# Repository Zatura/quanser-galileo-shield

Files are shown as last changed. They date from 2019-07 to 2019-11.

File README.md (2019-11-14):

# quanser_galileo_shield
Controlling a high-power quanser robotic arm with a hand-made Galileo compatible shield.  
PCB project design and simulation were made using proteus  https://www.labcenter.com/pcb/  
Shield Schematic  
Report (portuguese)  
  
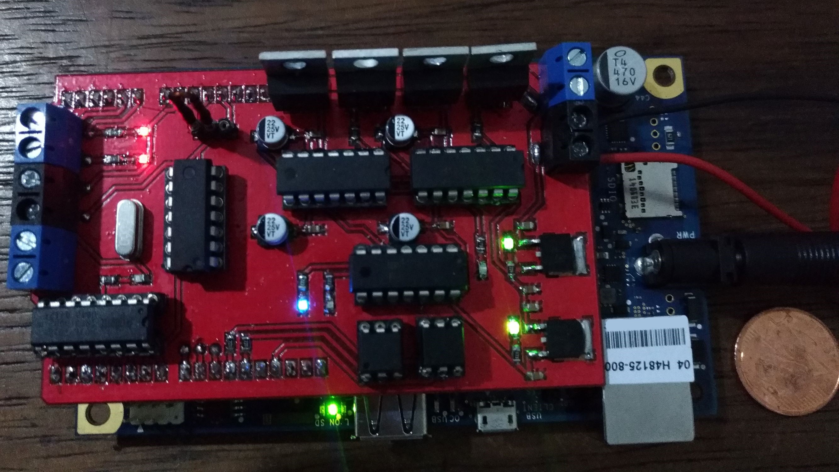
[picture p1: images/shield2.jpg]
shield
 

### Bare Copper PCB  
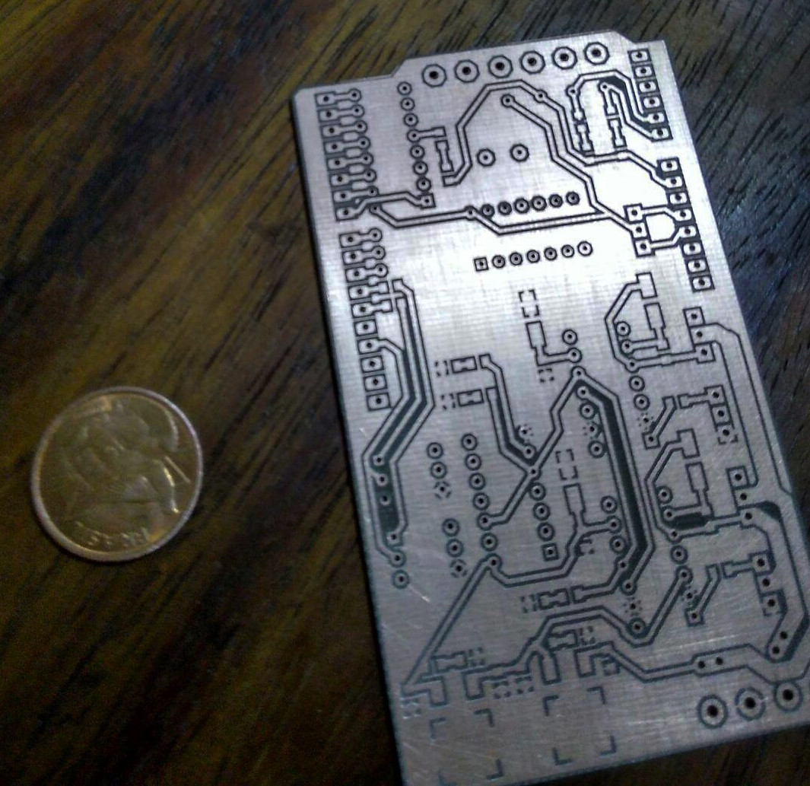
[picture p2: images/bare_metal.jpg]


### UV Masking(red tint)   
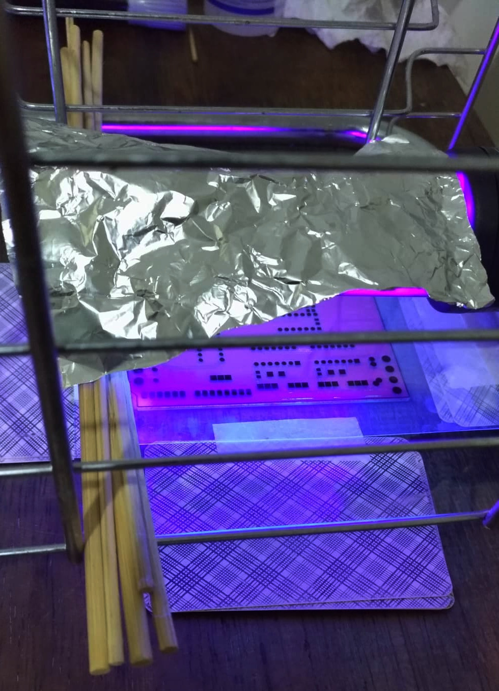
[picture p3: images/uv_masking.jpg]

  
# Use and Compilation
Compile using `make`  
After compilation success, executable `qmotion` should be at `/bin` folder 
 
```
qmotion - quanser motion

USAGE
	qmotion [options] input file

DESCRIPTION
	qmotion is a quanser robotic arm controller

OPTIONS
	-v, --version
		Prints qmotion version
    
	-h, --help
		Prints this help message

	-m VOLTAGE TIME, --move VOLTAGE TIME
		Moves the quanser robotic arm using VOLTAGE(-27 to 27) during TIME seconds 

	-t ANGLE, --target ANGLE 
		Moves the quanser robotic arm to the target at ANGLE degrees 

	-d, --decoder
		Reads and shows decoder and limit switch status

	-r, --reset
		Resets decoder register

	-p P I D, --pid P I D 
		Sets Proportional(P), Integrative(I) and Derivative(D) gains, saved at pid.dat file
    
	--no-color
		Does not use colors for printing
```    
    
# Examples

https://link.springer.com/content/pdf/10.1007/978-1-4302-6838-3_14.pdf

# Pins

IO0: D7 (encoder bit 7)  
IO1: D6 (encoder bit 6)  
IO2: D5 (encoder bit 5)  
IO3: D4 (encoder bit 4)  
IO4: D3 (encoder bit 3)  
IO5: D2 (encoder bit 2)  
IO6: D1 (encoder bit 1)  
IO7: D0 (encoder bit 0)  

IO8 :  !RST (Reset for 16-bits encoder register)  
IO9 :  !OE (Enable, activates the tristate buffer from the register)  
IO10 :  SEL (Selector for 16-bits encoder high or low byte in register)  
IO11:  PWM (pulse modulation width)  
IO12: SD (bridge-drivers shutdown)  
IO14: LMT_SWT2 (arm limit-sensor input)  
IO15: LMT_SWT1 (arm limit-sensor input)

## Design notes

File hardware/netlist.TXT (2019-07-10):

ISIS SCHEMATIC DESCRIPTION FORMAT 8.0
=====================================
Design:   H-bridge
Doc. no.: <NONE>
Revision: <NONE>
Author:   Arthur, Daniel e Matheus
Created:  25/06/2019
Modified: 25/06/2019

*PROPERTIES,0    

*MODELDEFS,0    

*PARTLIST,67   
A,LED-BLUE,LED-BLUE,BV=4V,DRIVE=1,EID=25,IMAX=30mA,PACKAGE=0805,ROFF=100k,RS=3,TLITMIN=0.1m,VF=3V
B,LED-BLUE,LED-BLUE,BV=4V,DRIVE=1,EID=24,IMAX=30mA,PACKAGE=0805,ROFF=100k,RS=3,TLITMIN=0.1m,VF=3V
C1,PCELEC22U16V75M,22uF,CODE="Digikey P5135-ND",EID=20,PACKAGE=ELECT-5
C2,CAP,100nF,EID=5,PACKAGE=0805_CAP
C3,CAP,100nF,EID=8,PACKAGE=0805_CAP
C4,PCELEC22U16V75M,22uF,CODE="Digikey P5135-ND",EID=22,PACKAGE=ELECT-5
C5,PCELEC22U16V75M,22uF,CODE="Digikey P5135-ND",EID=E,PACKAGE=ELECT-5
C6,CAP,100nF,EID=F,PACKAGE=0805_CAP
C7,CAP,100nF,EID=4,PACKAGE=0805_CAP
C8,PCELEC22U16V75M,22uF,CODE="Digikey P5135-ND",EID=B,PACKAGE=ELECT-5
C9,CAP,330nF,EID=3E,PACKAGE=0805_CAP
C10,CAP,100nF,EID=3F,PACKAGE=0805_CAP
C11,CAP,330nF,EID=41,PACKAGE=0805_CAP
C12,CAP,100nF,EID=40,PACKAGE=0805_CAP
C13,CERAMIC22P,22pF,CODE="Maplin WX48C",EID=2B,PACKAGE=0805_CAP
C14,CERAMIC22P,22pF,CODE="Maplin WX48C",EID=2C,PACKAGE=0805_CAP
D1,1N4007,1N4007,EID=1,PACKAGE=DO214
D2,1N4007,1N4007,EID=C,PACKAGE=DO214
D3,LED-GREEN,LED-GREEN,BV=4V,DRIVE=1,EID=44,IMAX=20mA,PACKAGE=0805,ROFF=100k,RS=3,TLITMIN=0.1m,VF=2V
D4,LED-GREEN,LED-GREEN,BV=4V,DRIVE=1,EID=43,IMAX=20mA,PACKAGE=0805,ROFF=100k,RS=3,TLITMIN=0.1m,VF=2V
J1,ARDUINO-SIL8,ARDUINO-SIL8,EID=4F,PACKAGE=ARDUINO-SIL8
J2,ARDUINO-SIL10,ARDUINO-SIL10,EID=52,PACKAGE=ARDUINO-SIL10
J3,ARDUINO-SIL6,ARDUINO-SIL6,EID=50,PACKAGE=ARDUINO-SIL6
J4,ARDUINO-SIL8,ARDUINO-SIL8,EID=51,PACKAGE=ARDUINO-SIL8
J5,TBLOCK-M2,TBLOCK-M2,EID=18,PACKAGE=TBLOCK-M2
J6,TBLOCK-M2,TBLOCK-M2,EID=16,PACKAGE=TBLOCK-M2
J6_MOTOR,TBLOCK-M2,TBLOCK-M2,EID=29,PACKAGE=TBLOCK-M2
J7,TBLOCK-M2,TBLOCK-M2,EID=26,PACKAGE=TBLOCK-M2
J8,TBLOCK-M2,TBLOCK-M2,EID=10,PACKAGE=TBLOCK-M2
JP1,JUMPER2,JUMPER2,EID=2E,PACKAGE=CONN-SIL3,ROFF=100M,RON=0.01,STATE=0,TSWITCH=1m
LMT1,LED-GREEN,LED-RED,BV=4V,DRIVE=1,EID=1A,IMAX=20mA,PACKAGE=0805,ROFF=100k,RS=3,TLITMIN=0.1m,VF=2V
LMT2,LED-GREEN,LED-RED,BV=4V,DRIVE=1,EID=4B,IMAX=20mA,PACKAGE=0805,ROFF=100k,RS=3,TLITMIN=0.1m,VF=2V
Q1,IRFZ44N,IRFZ44N,EID=11,PACKAGE=TO220,SPICELIB=IRPOWER,SPICEMODEL=irfz44n,SPICEPINS="D,G,S"
Q2,IRFZ44N,IRFZ44N,EID=12,PACKAGE=TO220,SPICELIB=IRPOWER,SPICEMODEL=irfz44n,SPICEPINS="D,G,S"
Q3,IRFZ44N,IRFZ44N,EID=19,PACKAGE=TO220,SPICELIB=IRPOWER,SPICEMODEL=irfz44n,SPICEPINS="D,G,S"
Q4,IRFZ44N,IRFZ44N,EID=1F,PACKAGE=TO220,SPICELIB=IRPOWER,SPICEMODEL=irfz44n,SPICEPINS="D,G,S"
R1,RES,10R,EID=14,PACKAGE=0805_RES,PRIMTYPE=RESISTOR
R2,RES,10R,EID=15,PACKAGE=0805_RES,PRIMTYPE=RESISTOR
R3,RES,10R,EID=9,PACKAGE=0805_RES,PRIMTYPE=RESISTOR
R4,RES,10R,EID=6,PACKAGE=0805_RES,PRIMTYPE=RESISTOR
R5,RES,220KR,EID=45,PACKAGE=0805_RES,PRIMTYPE=RESISTOR
R6,RES,47KR,EID=42,PACKAGE=0805_RES,PRIMTYPE=RESISTOR
R7,RES,10KR,EID=4D,PACKAGE=0805_RES,PRIMTYPE=RESISTOR
R8,RES,1MR,EID=2D,PACKAGE=0805_RES,PRIMTYPE=RESISTOR
R9,RES,10kR,EID=13,PACKAGE=0805_RES,PRIMTYPE=RESISTOR
R11,RES,10kR,EID=17,PACKAGE=0805_RES,PRIMTYPE=RESISTOR
R13,RES,47KR,EID=1B,PACKAGE=0805_RES,PRIMTYPE=RESISTOR
R14,RES,47KR,EID=1E,PACKAGE=0805_RES,PRIMTYPE=RESISTOR
R15,RES,22KR,EID=21,PACKAGE=0805_RES,PRIMTYPE=RESISTOR
R16,RES,22KR,EID=23,PACKAGE=0805_RES,PRIMTYPE=RESISTOR
R19,RES,220R,EID=28,PACKAGE=0805_RES,PRIMTYPE=RESISTOR
R20,RES,220R,EID=32,PACKAGE=0805_RES,PRIMTYPE=RESISTOR
R23,RES,10KR,EID=2A,PACKAGE=0805_RES,PRIMTYPE=RESISTOR
R24,RES,470kR,EID=49,PACKAGE=0805_RES,PRIMTYPE=RESISTOR
R25,RES,470kR,EID=4A,PACKAGE=0805_RES,PRIMTYPE=RESISTOR
RST,LED-GREEN,LED-GREEN,BV=4V,DRIVE=1,EID=1C,IMAX=20mA,PACKAGE=0805,ROFF=100k,RS=3,TLITMIN=0.1m,VF=2V
SD,LED-GREEN,LED-GREEN,BV=4V,DRIVE=1,EID=4C,IMAX=20mA,PACKAGE=0805,ROFF=100k,RS=3,TLITMIN=0.1m,VF=2V
U1,IR2110,IR2110,EID=A,ITFMOD=IR2112ITF,PACKAGE=DIL14
U2,IR2110,IR2110,EID=D,ITFMOD=IR2112ITF,PACKAGE=DIL14
U3,7812,7812,EID=3D,PACKAGE=DPAK
U4,7805,7805,EID=3C,PACKAGE=DPAK
U5,74LS04,74LS04,EID_E=7,GND=GND3,ITFMOD=TTLLS,PACKAGE=DIL14,VCC=VDD_GALILEO
U7,4N25,4N25,EID=2,PACKAGE=DIL06
U8,4N25,4N25,EID=3,PACKAGE=DIL06
U9,74LS04,74LS04,EID_A=35,EID_C=39,EID_D=36,ITFMOD=TTLLS,MODFILE=74INV.MDF,PACKAGE=DIL14
U10,HCTL2016,HCTL2016,EID=1D,PACKAGE=DIL16
X1,CRYSTAL,CRYSTAL,EID=27,FREQ=1MHz,PACKAGE=XTAL18

*NETLIST,71   
#00000,6
C3,PS,2
C4,PS,-
Q1,PS,3
Q2,PS,2
J6_MOTOR,PS,1
U1,PS,5

#00001,4
C3,PS,1
D1,PS,K
U1,PS,6
C4,PS,+

#00008,2
R1,PS,1
U1,PS,7

#00009,2
R1,PS,2
Q1,PS,1

#00010,2
R2,PS,1
U1,PS,1

#00011,2
R2,PS,2
Q2,PS,1

#00012,6
Q3,PS,2
Q4,PS,3
C8,PS,-
C7,PS,2
U2,PS,5
J6_MOTOR,PS,2

#00013,2
Q3,PS,1
R3,PS,2

#00014,2
Q4,PS,1
R4,PS,2

#00018,4
C7,PS,1
D2,PS,K
U2,PS,6
C8,PS,+

#00023,2
R4,PS,1
U2,PS,7

#00024,2
R3,PS,1
U2,PS,1

#00030,2
R7,PS,1
LMT1,PS,1

#00036,2
R23,PS,1
LMT2,PS,1

#00044,2
R6,PS,1
D4,PS,1

#00045,2
D3,PS,1
R5,PS,2

#00051,2
U7,PS,1
R19,PS,2

#00054,3
U7,PS,5
R9,PS,2
U9,IP,13

#00055,2
U7,PS,6
R24,PS,1

#00057,2
U8,PS,1
R20,PS,2

#00060,3
U8,PS,5
R11,PS,2
U9,IP,1

#00061,2
U8,PS,6
R25,PS,1

#00066,2
R13,PS,1
SD,PS,1

#00068,2
R14,PS,1
RST,PS,1

#00070,2
R15,PS,1
B,PS,1

#00071,2
R16,PS,1
A,PS,1

#00110,1
J3,PS,3

#00111,1
J3,PS,4

#00112,1
J3,PS,5

#00113,1
J3,PS,6

#00114,1
J4,PS,1

#00115,1
J4,PS,2

#00116,1
J4,PS,3

#00119,1
J4,PS,6

#00121,1
J4,PS,8

#00126,1
J2,PS,1

#00127,1
J2,PS,2

#00128,1
J2,PS,3

#00130,1
J2,PS,5

#00132,4
X1,PS,1
C13,PS,2
R8,PS,1
U5,IP,11

SOURCE_12,10
SOURCE_12,OT
U4,IP,2
C11,PS,2
U3,PS,3
C10,PS,2
R5,PS,1
D2,PS,A
U2,PU,3
D1,PS,A
U1,PU,3

SOURCE_27,6
SOURCE_27,OT
J8,PS,2
U3,IP,2
C9,PS,2
Q4,PS,2
Q1,PS,2

A,6
A,OT
R16,PS,2
U9,IP,5
U9,OP,12
U2,IP,10
U1,IP,12

B,5
B,OT
R15,PS,2
U9,OP,6
U2,IP,12
U1,IP,10

{NC},8
U8,PS,3
U7,PS,3
U2,PS,4
U2,PS,8
U2,PS,14
U1,PS,4
U1,PS,8
U1,PS,14

SD,5
SD,OT
R13,PS,2
U9,OP,2
U2,IP,11
U1,IP,11

D0,3
D0,OT
J1,PS,1
U10,OP,1

D1,3
D1,OT
J1,PS,2
U10,OP,15

D2,3
D2,OT
J1,PS,3
U10,OP,14

D3,3
D3,OT
J1,PS,4
U10,OP,13

D4,3
D4,OT
J1,PS,5
U10,OP,12

D5,3
D5,OT
J1,PS,6
U10,OP,11

D6,3
D6,OT
J1,PS,7
U10,OP,10

D7,3
D7,OT
J1,PS,8
U10,OP,9

LMT2,4
LMT2,OT
J3,PS,1
R23,PS,2
J6,PS,2

LMT1,4
LMT1,OT
J3,PS,2
R7,PS,2
J6,PS,1

OE,3
OE,OT
J2,PS,9
U10,IP,4

RST,4
RST,OT
J2,PS,10
U10,IP,5
R14,PS,2

GPIO_PWM,3
GPIO_PWM,OT
J2,PS,7
R19,PS,1

SEL,3
SEL,OT
J2,PS,8
U10,IP,3

GPIO_SD,3
GPIO_SD,OT
J2,PS,6
R20,PS,1

CLK,6
CLK,OT
X1,PS,2
C14,PS,2
R8,PS,2
U5,OP,10
U10,IP,2

CH A,3
CH A,OT
J5,PS,1
U10,IP,7

CH B,3
CH B,OT
J5,PS,2
U10,IP,6

VDD5,3
VDD5,OT
JP1,PS,1
J4,PS,5

VDD3,3
VDD3,OT
JP1,PS,3
J4,PS,4

GND,28,CLASS=GND
GND,PR
R25,PS,2
R24,PS,2
U9,PP,7
B,PS,2
A,PS,2
SD,PS,2
U8,PS,4
U7,PS,4
J8,PS,1
U3,PP,1
C9,PS,1
C10,PS,1
D3,PS,2
U4,PP,1
C11,PS,1
C12,PS,1
D4,PS,2
C5,PS,-
C6,PS,2
U2,PP,13
U2,PP,2
C1,PS,-
C2,PS,2
U1,PP,13
Q2,PS,3
Q3,PS,3
U1,PP,2

GND2,4,CLASS=GND
GND2,PR
J2,PS,4
U8,PS,2
U7,PS,2

GND3,10,CLASS=GND
GND3,PR
J7,PS,1
U5,PP,7
C13,PS,1
C14,PS,1
J4,PS,7
U10,IP,8
RST,PS,2
LMT2,PS,2
LMT1,PS,2

VCC/VDD,15,CLASS=POWER
VCC,PT
VCC/VDD,PR
SOURCE_5,OT
U9,PP,14
R11,PS,1
R9,PS,1
U4,PS,3
C12,PS,2
R6,PS,2
C5,PS,+
C6,PS,1
U2,PP,9
C1,PS,+
C2,PS,1
U1,PP,9

VDD_GALILEO,5,CLASS=GND
VDD_GALILEO,PR
JP1,PS,2
J7,PS,2
U5,PP,14
U10,IP,16

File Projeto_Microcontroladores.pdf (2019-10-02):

## Confecçao de um Shield para a Galileo Gen 2 para o ˜ Acionamento das Juntas e Leitura dos Sensores do Robô 2DSFJE

Arthur Ribeiro¹

, Daniel Cunha¹

, Matheus Tura¹

1
Instituto de Informatica – Universidade Federal do Rio Grande do Sul (UFRGS) ´ Caixa Postal 15.064 – 91.501-970 – Porto Alegre – RS – Brazil

{aribeiro, dmcunha, mttura}@inf.ufrgs.br

Resumo. Este documento descreve o processo para a criaçao de um shield para ˜ a placa Intel Galileo Gen 2. Este hardware e capaz de acionar o motor e ler os ´
sensores presentes no robo Quanser 2DSFJE. Ao longo do documento ser ˆ | a des- ´
crito o processo de todas as etapas de desenvolvimento deste hardware, desde
de sua etapa inicial de concepçao at ˜ | e a etapa final de implementaç ´ | ao. ˜

### 1. Introduçaõ

O projeto proposto consiste no desenvolvimento e confecçao de um shield para a Intel Ga- ˜ lileo Gen 2, o shield deve ser capaz de acionar uma das juntas do robo Quanser 2DSFJE, a ˆ
junta possui um motor com encoder, para o acionamento e necess ´ | ario fornecer uma tens ´ | aõ
entre -27 e 27 volts, o shield deve implementar uma ponte h que controla o valor medio ´
desta tensao atrav ˜ | es de um sinal pwm. O ciclo de trabalho deste pwm representa o sen- ´
tido e velocidade do movimento do motor, onde o ciclo de trabalho em 0% corresponde ao motor girando em velocidade maxima em um sentido, o ciclo de trabalho em 50% ´ corresponde ao motor parado, o ciclo de trabalho em 100% corresponde ao motor girando
em velocidade maxima no sentido contr ´ | ario. O encoder do Quanser tamb ´ | em deve ser ´
decodificado pelo shield, para decodificar quadratura, foi utilizado um circuito integrado decodificador de quadratura, para que nao haja erro na contagem e consequentemente ˜ dados inconsistentes.

Concomitantemente com o desenvolvimento do shield, deve-se desenvolver um software que implemente um controlador PID. O software deve incluir uma biblioteca com uma API. Com a API deve ser possível ler o valor do encoder em radianos, comandar do motor em Volts e a leitura do sensor de fim de curso. A biblioteca deve ser desenvolvida para executar no Linux como um programa no espaço de usuario, sem pri- ´
vilegios de superusu ´ | ario. Os pr ´ | oximos cap ´ | ítulos detalharao o funcionamento do hardware ˜
e do software desenvolvido.

### 2. Hardware

Para possibilitar o controle a junta do Quanser utilizando a Galileo Gen 2, se desenvolveu um shield utilizando uma placa de circuito impresso. O shield possui dois circuitos distintos, um deles implementa uma ponte H que possui toda parte de alta potencia do shield, o outro circuito implementa o decodificador de quadratura.

Alem disso, para maior parte do circuito foi optado por componentes SMD, devido ´ ao seu menor tamanho e tambem menores problemas de mal contato, e praticidade na hora ´

da soldagem. O tamanho escolhido de SMDS para capacitores, resistores e LEDs foi de 0805, nao foi escolhido abaixo deste tamanho, pois abaixo desse tamanho a dificuldade ˜ de solda poderia aumentar consideravelmente.

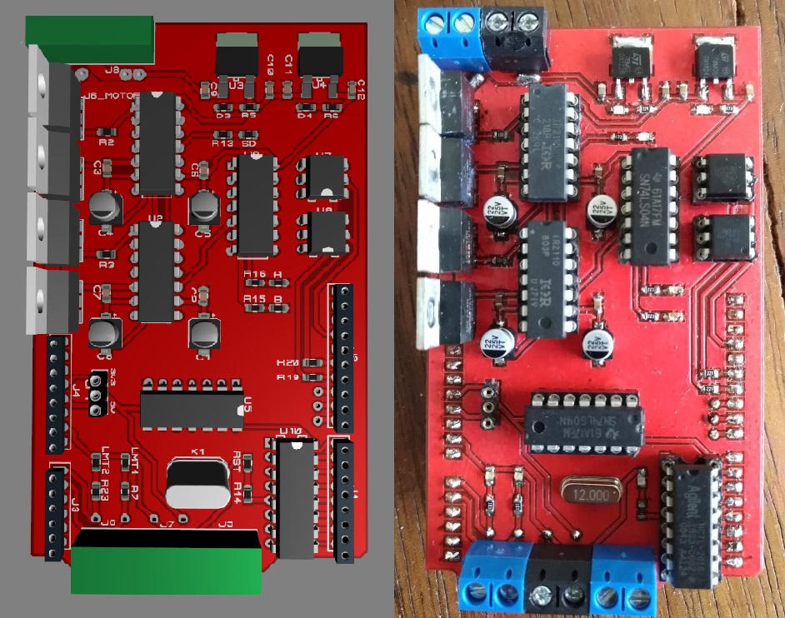
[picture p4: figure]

Figura 1. Ao lado esquerdo, simulaçao, ao direito, shield físico ˜

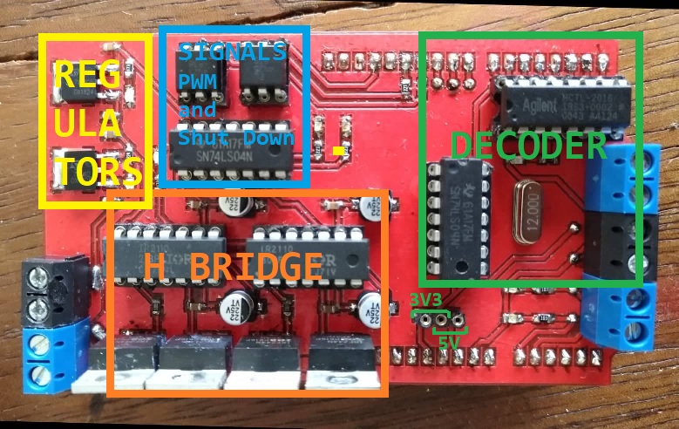
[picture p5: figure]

Figura 2. Blocos basicos ´

### 3. Alimentaçao e Reguladores ˜

A Ponte H necessita de alimentaçao de 5V para controle l ˜ | ogico, e 12V para carregamento ´
dos capacitores de bootstrap, para isso, um regulador LM7805 foi utilizado para gerar os 5V e um LM7812 para gerar os 12V. o Regulador LM7812 tem seu input conectado com o terminal de 27V da fonte Quanser, enquanto, para fins de reduzir a queda de tensaõ do LM7805, este tem seu input conectado na saída do LM7812. A corrente que passa LM7812 e a corrente dos capacitores, mais a corrente do LM7805, que tem sua maior ´ potencia gasta com LEDs. Logo, devido a baixa corrente, foi escolhido componentes ˆ reguladores em SMD, com sua dissipaçao no plano terra, visto que como receberiam ˜ pouca corrente, esquentariam pouco.

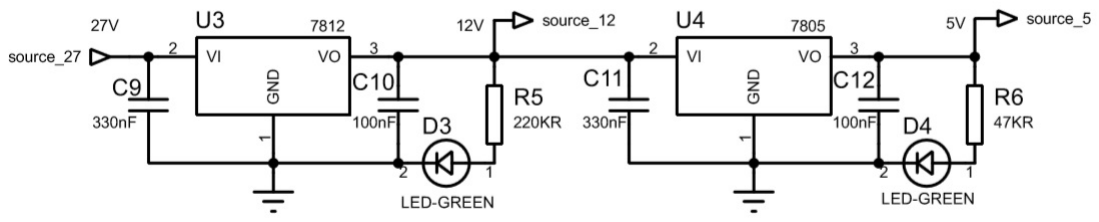
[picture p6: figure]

Figura 3. Reguladores de tensao 12V e 5V ˜

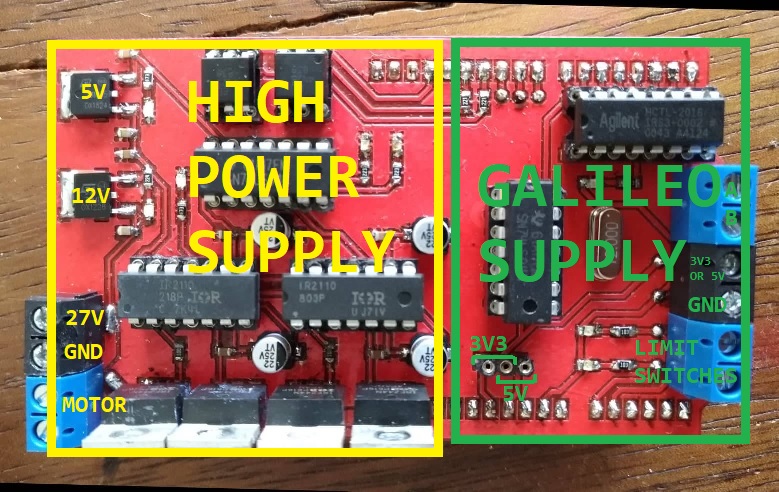
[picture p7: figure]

Figura 4. Separaçao da alimentaç ˜ | aõ

### 4. Optoisolamento

Para que que os sinais de controle da ponte H (pwm e shutdown) nao tivessem ˜
sua alimentaçao misturada com a alimentaç ˜ | ao de pot ˜ | encia, foram utilizados 2 opto- ˆ
acopladores 4N25 para isolar os dois circuitos, a imagem abaixo demonstra a separaçaõ do optoisolamento.

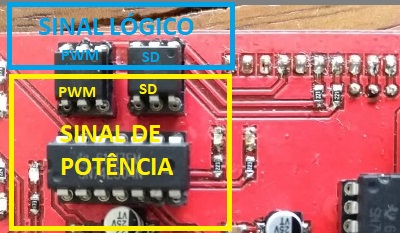
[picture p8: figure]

Figura 5. Imagem real dos optoacopladores nos sockets do shield

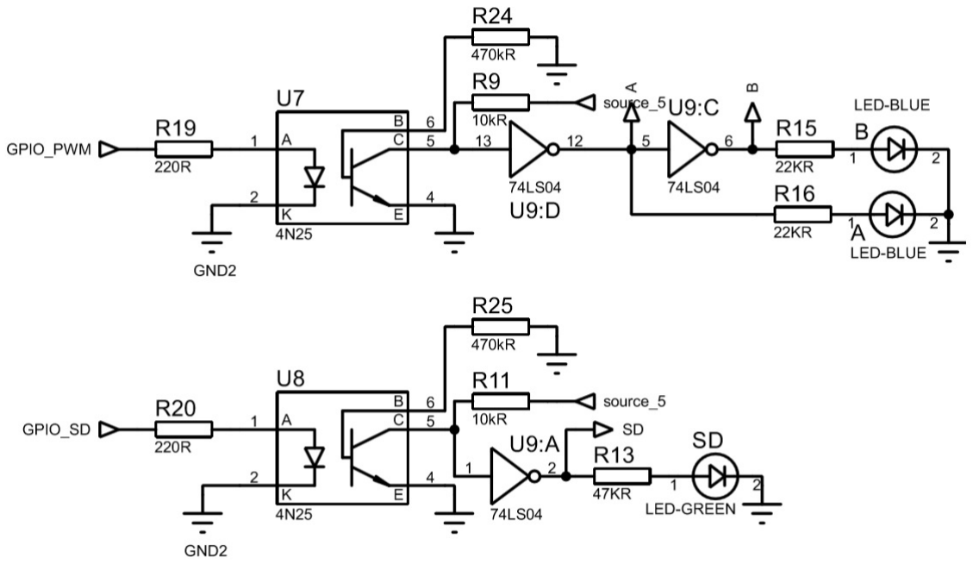
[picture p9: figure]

Figura 6. esquematico do circuito de opto-isolamento ´

### 5. Ponte H

Pelo fato do motor da junta Quanser ter um consumo de corrente maximo maior que 1A, ´
o cuidado com a dissipaçao devido a pot ˜ | encia din ˆ | amica do chaveamento dos transisto- ˆ
res de potencia deve ser redobrado, para isso, os MOSFETs escolhidos para chavear a ˆ ponte H sao todos do tipo NMOS, que naturalmente possuem velocidade de chaveamento ˜ maior que na família PMOS. Este modelo de ponte-H NMOS-only, possui menor potencia ˆ dinamica que uma ponte H convencional que utiliza PMOS na rede pull-up. ˆ

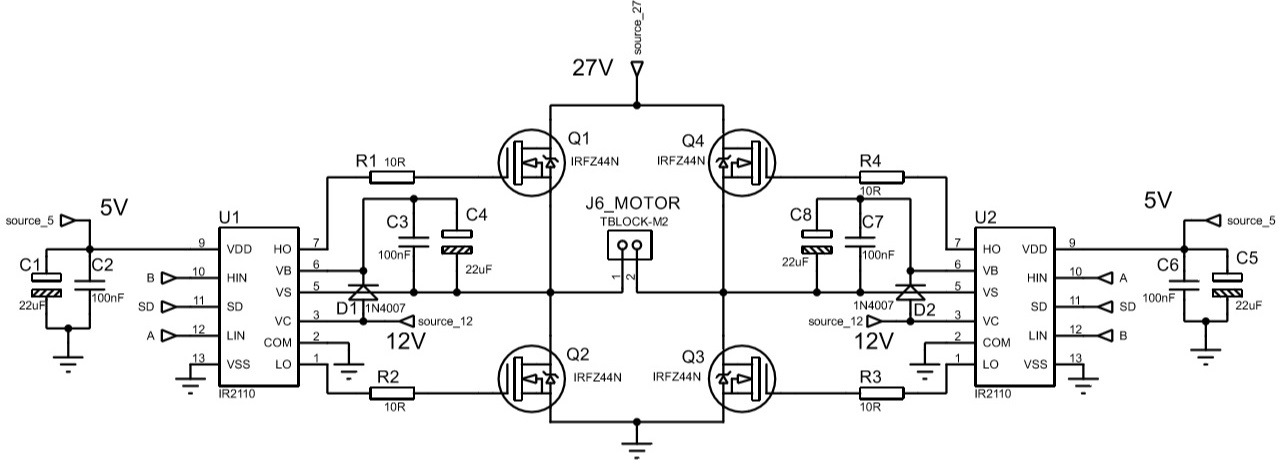
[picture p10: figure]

Figura 7. Ponte H NMOS

### 5.1. Capacitores de bootstrap

Para que um NMOS atinja a zona de saturaçao, a tens ˜ | aõ V gs deve ser maior que a tensaõ
de threshold V th satisfazendo as seguintes equaçoes abaixo. ˜

V gs > V th

V ds > V gs − V th

Porem os transistores da rede pull-up(Q1 e Q4, Figura 7) em uma rede NMOS- ´
only nao acionam corretamente, visto que seus sources est ˜ | ao conectados nos terminais ˜
do motor, ao inves de GND. Esta tens ´ | aõ V s, durante o acionamento dos gates, alem de ´
ser flututante em alguns períodos, em outros, e uma tens ´ | ao maior que o terminal de gate, ˜
nao entrando na zona de saturaç ˜ | ao descrita na equaç ˜ | ao acima. Isso al ˜ | em de causar mal ´
funcionamento, superaquece a rede pull-up, muitas vezes, queimando-a.
| Para que o problema acima nao ocorra e a tens ˜ | | aõ V gs seja maior que a tensaõ
V th, e usada uma t ´ | ecnica de bootstrapping, onde s ´ | ao utilizados capacitores de 22uF(C4 e ˜
C8, Figura 7) em serie com source dos MOSFETS da rede pull-up, conectado-os ao gate. ´
A corrente de carregamento destes capacitores advem de de um regulador de 12V atrav ´ | es´
de um diodo que garante a carga do capacitor, tais capacitores carregam uma tensao su- ˜ ficiente que somadas a tens ` aõ V s de source, sao mais que suficientes para ultrapassar o ˜ V th, polarizando e saturando corretamente a rede pull-up durante o chaveamento.

Por fins de simplificaçao deste processo de bootstrap, o ciclo de carregamento e ˜ descarregamento destes capacitores e feito pelos CIs de bridge-driver IR2110, utilizados ´ propriamente para isso.

### 6. Leitura de quadraturas do Decoder HTCL2016

O HTCL2016 e um encoder de 16 bits, mas que possui 8 pinos de sa ´ | | | ída para leitura, estes
pinos sao os bits do registrador/contador de quadraturas. Sua entrada de Clock ˜ | e do tipo ´
schmidtt-trigger, e portanto com apenas um simples oscilador Pierce foi necessario para ´ o correto funcionamento do decoder.

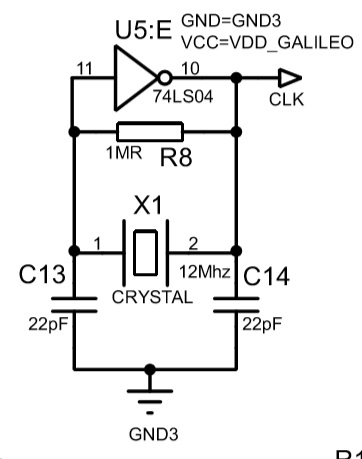
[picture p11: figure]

Figura 8. Esquematico do Oscilador Pierce ´

Alem destes pinos, o decoder possui um pino de RST e um pino de Seleç ´ | ao(SEL) ˜
para selecionar entre o byte mais significativo ou menos significativo, porem para que ´
a leitura seja feita corretamente, e necess ´ | ario acionar na ordem correeta o pino de !OE, ´
que e respons ´ | avel pelo acionamento dos buffer-tristates do registrador, permitindo que a ´
leitura seja feita sem interferir na continua contagem das quadraturas.

Abaixo, o diagrama de pulsos de sinais que mostram a ordem correta, como
tambem o tempo necess ´ | ario entre um edge e outro, para a correta leitura. ´

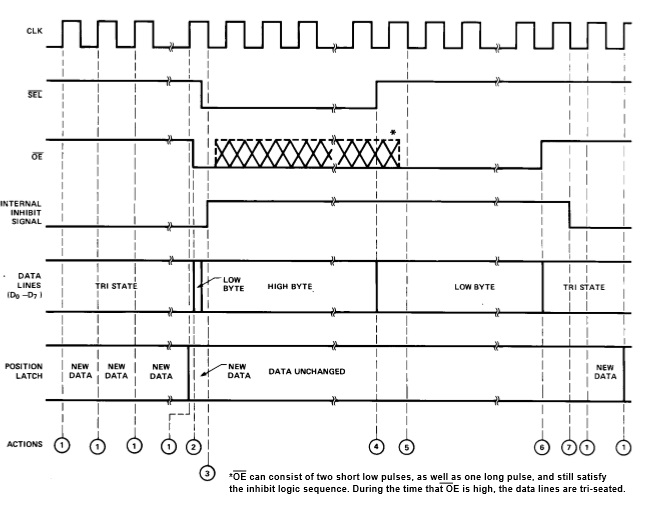
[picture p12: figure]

Figura 9. Diagrama de pulsos de sinais original do Datasheet

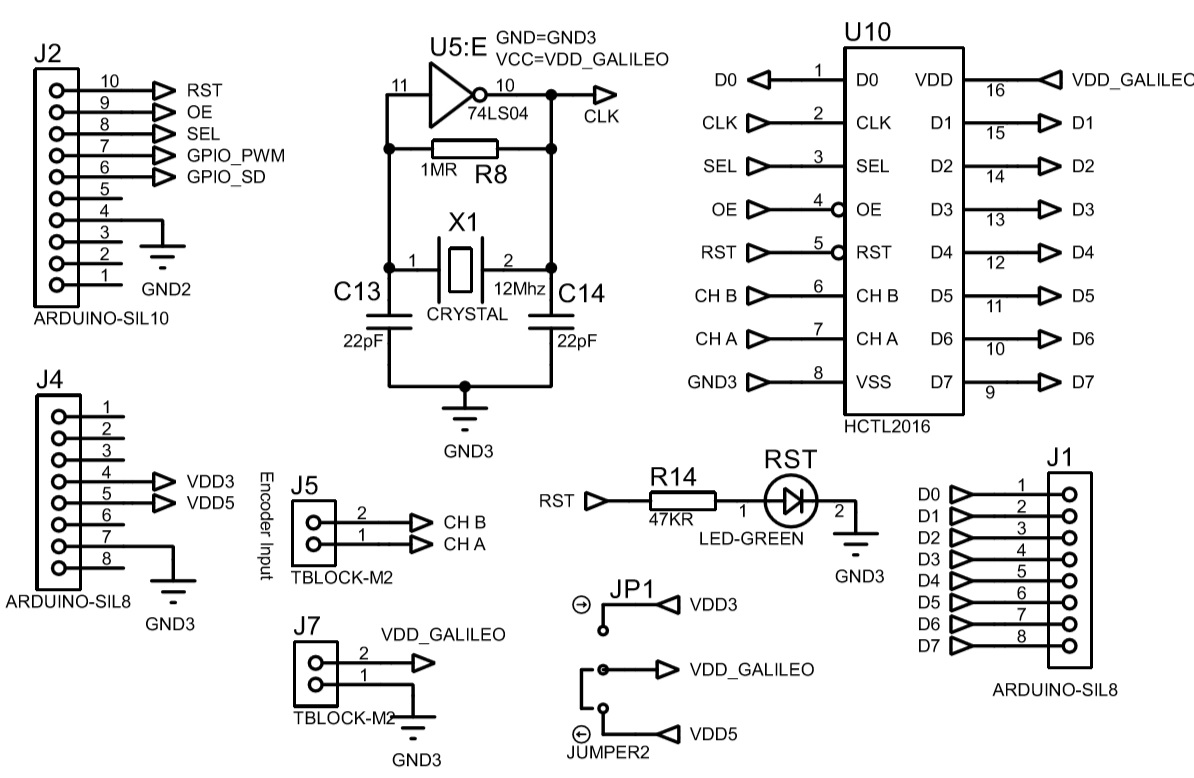
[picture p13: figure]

Figura 10. circuito de leitura de quadratura

### 7. Placa de Circuito Impresso

A placa de Circuito impresso, foi fresada no LASCAR, onde a CNC foi operada por Marcos Vizzotto.

Para obter a PCI sem erros, foram necessarios 3 projetos f ´ | ísicos de PCI, visto que
o projeto das duas primeiras eram mais difíceis de soldar e a disposiçao dos componentes ˜
nao era confort ˜ | avel. Abaixo est ´ | ao o top layer e bottom layer, como tamb ˜ | em o diagrama ´
colorido, onde azul representa a layer bottom e a vermelha, a layer top.

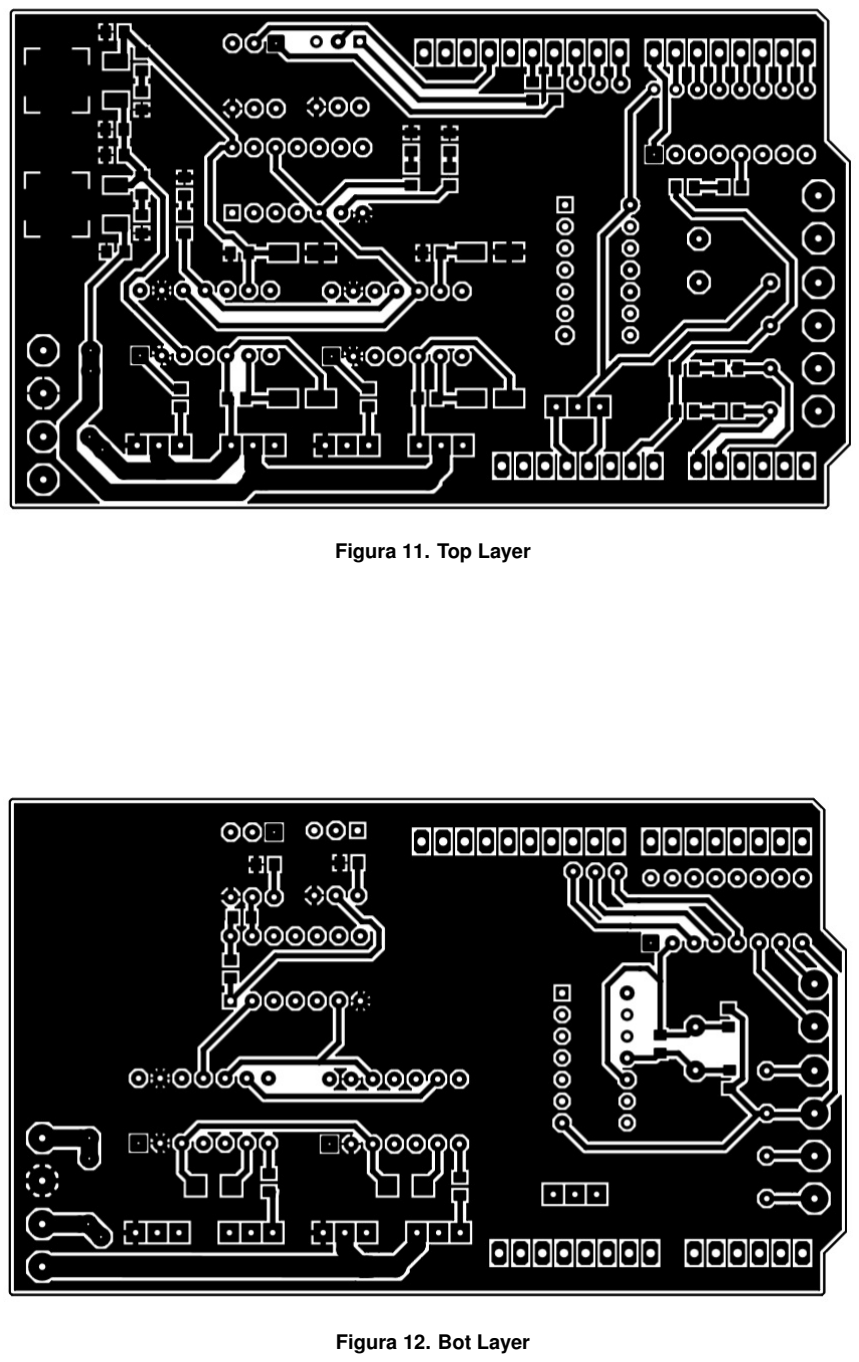
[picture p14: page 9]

Figura 11. Top Layer

Figura 12. Bot Layer

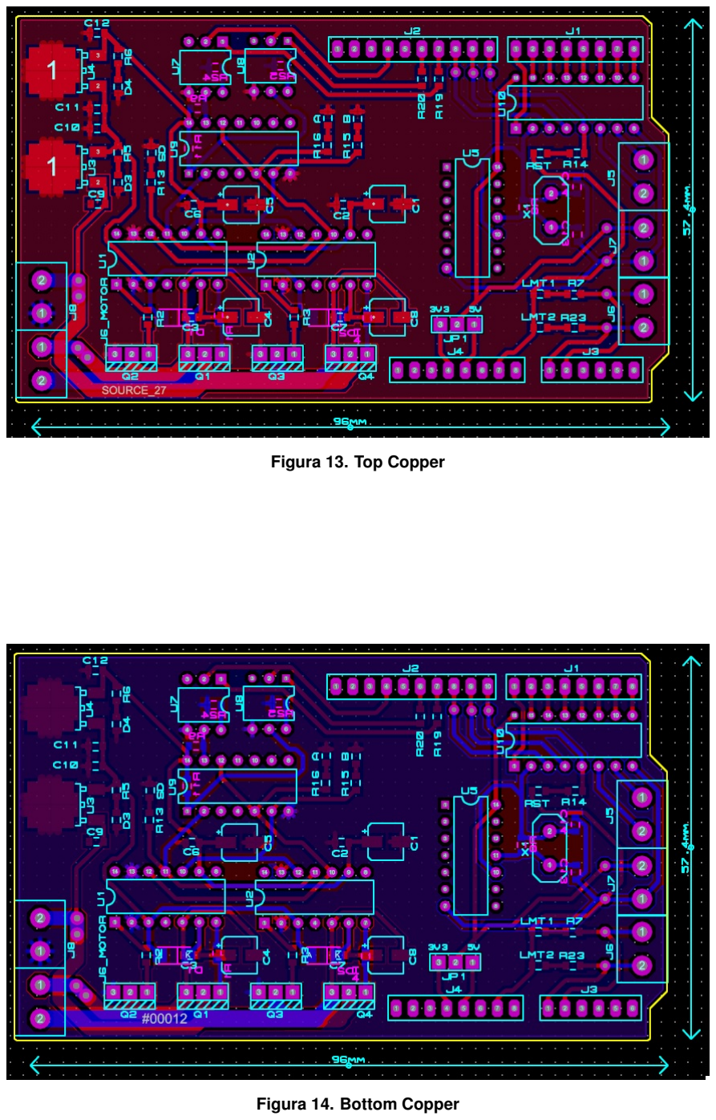
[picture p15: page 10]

Figura 13. Top Copper

Figura 14. Bottom Copper


Figura 15. Placa montada, em teste de decoder, com alimentaçao de pot ˜ | encia ˆ

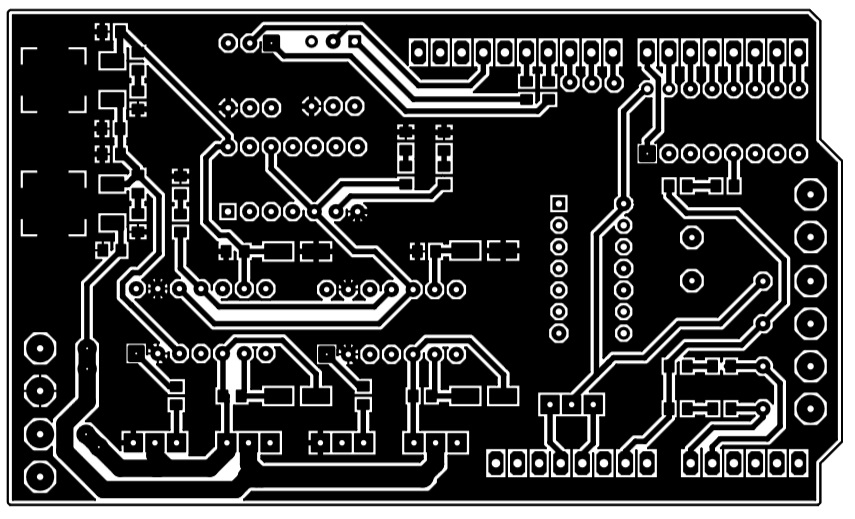
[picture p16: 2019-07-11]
images/top_layer.jpg

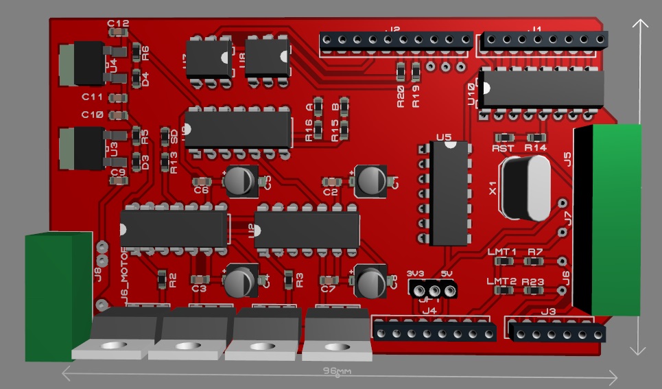
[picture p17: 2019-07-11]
images/top-view-3D.jpg

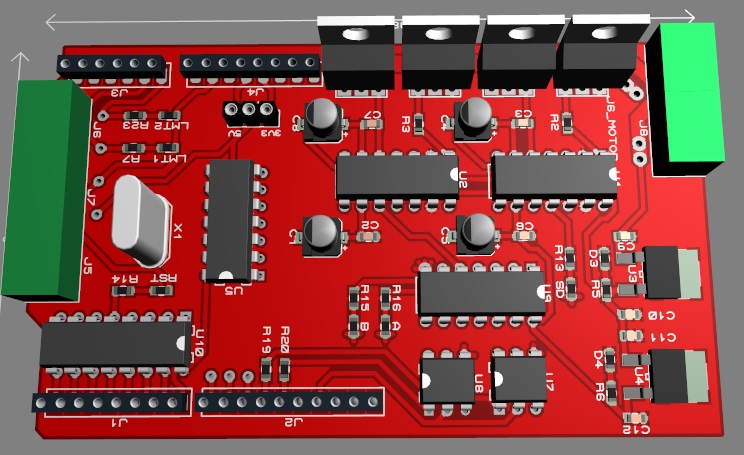
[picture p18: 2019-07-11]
images/simulation.jpg

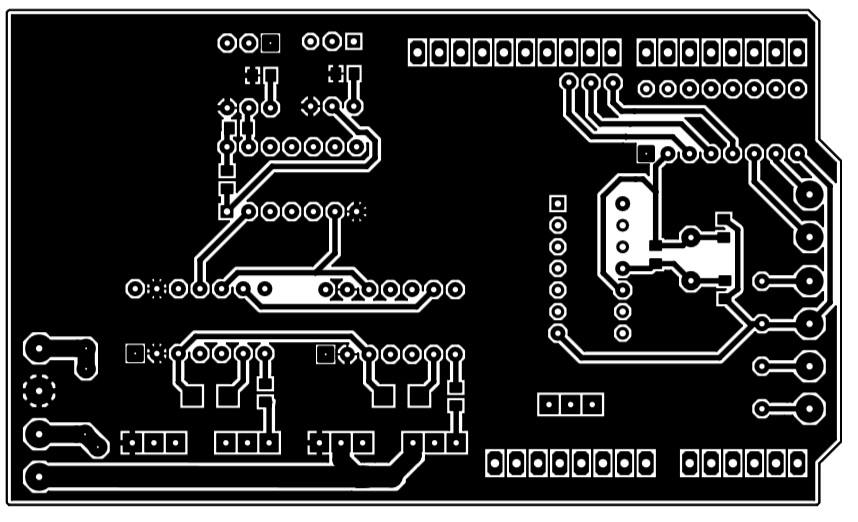
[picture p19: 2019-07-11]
images/bot_layer.jpg

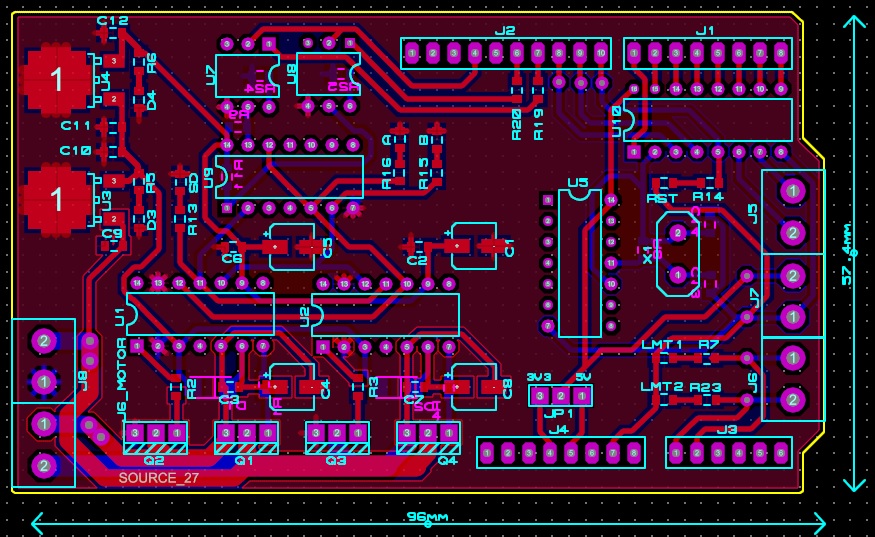
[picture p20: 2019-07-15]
images/red-layer.jpg

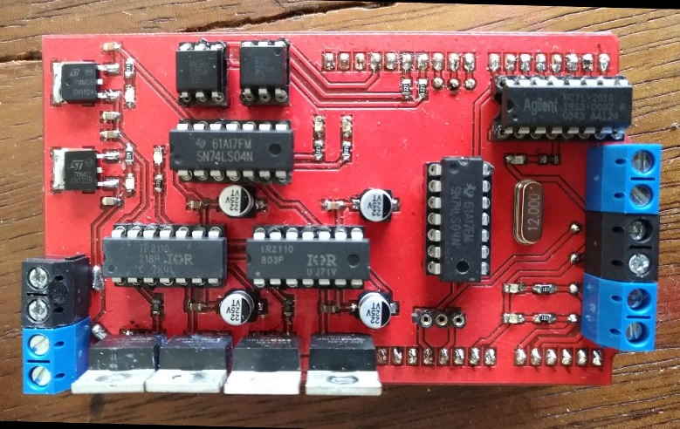
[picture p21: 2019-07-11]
images/top-view.jpg

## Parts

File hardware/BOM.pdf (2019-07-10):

## Bill Of Materials for H-bridge

Design Title | H-bridge
Author | Arthur, Daniel e Matheus

### Document Number Revision

Design Created | terça-feira, 25 de junho de 2019
Design Last Modified quarta-feira, 10 de julho de 2019

### Total Parts In Design 67

0 Modules
Quantity | References | Value | Stock Code | Unit Cost
Sub-totals: | | | | R$0,00
14 Capacitors
Quantity | References | Value | Stock Code | Unit Cost
4 | C1,C4-C5,C8 | 22uF | Digikey P5135-ND
6 | C2-C3,C6-C7,C10,C12 | 100nF
2 | C9,C11 | 330nF
2 | C13-C14 | 22pF | Maplin WX48C
Sub-totals: | | | | R$0,00
19 Resistors
Quantity | References | Value | Stock Code | Unit Cost
4 | R1-R4 | 10R
1 | R5 | 220KR
3 | R6,R13-R14 | 47KR
2 | R7,R23 | 10KR
1 | R8 | 1MR
2 | R9,R11 | 10kR
2 | R15-R16 | 22KR
2 | R19-R20 | 220R
2 | R24-R25 | 470kR
Sub-totals: | | | | R$0,00
9 Integrated Circuits
Quantity | References | Value | Stock Code | Unit Cost
2 | U1-U2 | IR2110
1 | U3 | 7812
1 | U4 | 7805
2 | U5,U9 | 74LS04
2 | U7-U8 | 4N25
1 | U10 | HCTL2016
Sub-totals: | | | | R$0,00
4 Transistors
Quantity | References | Value | Stock Code | Unit Cost
4 | Q1-Q4 | IRFZ44N
Sub-totals: | | | | R$0,00
4 Diodes
Quantity | References | Value | Stock Code | Unit Cost
2 | D1-D2 | 1N4007
2 | D3-D4 | LED-GREEN
Sub-totals: | | | | R$0,00
17 Miscellaneous
Quantity | References | Value | Stock Code | Unit Cost
2 | A,B | LED-BLUE
2 | J1,J4 | ARDUINO-SIL8
1 | J2 | ARDUINO-SIL10

1 | J3 | ARDUINO-SIL6
5 | J5-J8,J6_MOTOR | TBLOCK-M2
1 | JP1 | JUMPER2
2 | LMT1-LMT2 | LED-RED
2 | RST,SD | LED-GREEN
1 | X1 | CRYSTAL
Sub-totals: | R$0,00
Totals: | R$0,00

quarta-feira, 10 de julho de 2019 16:10:25

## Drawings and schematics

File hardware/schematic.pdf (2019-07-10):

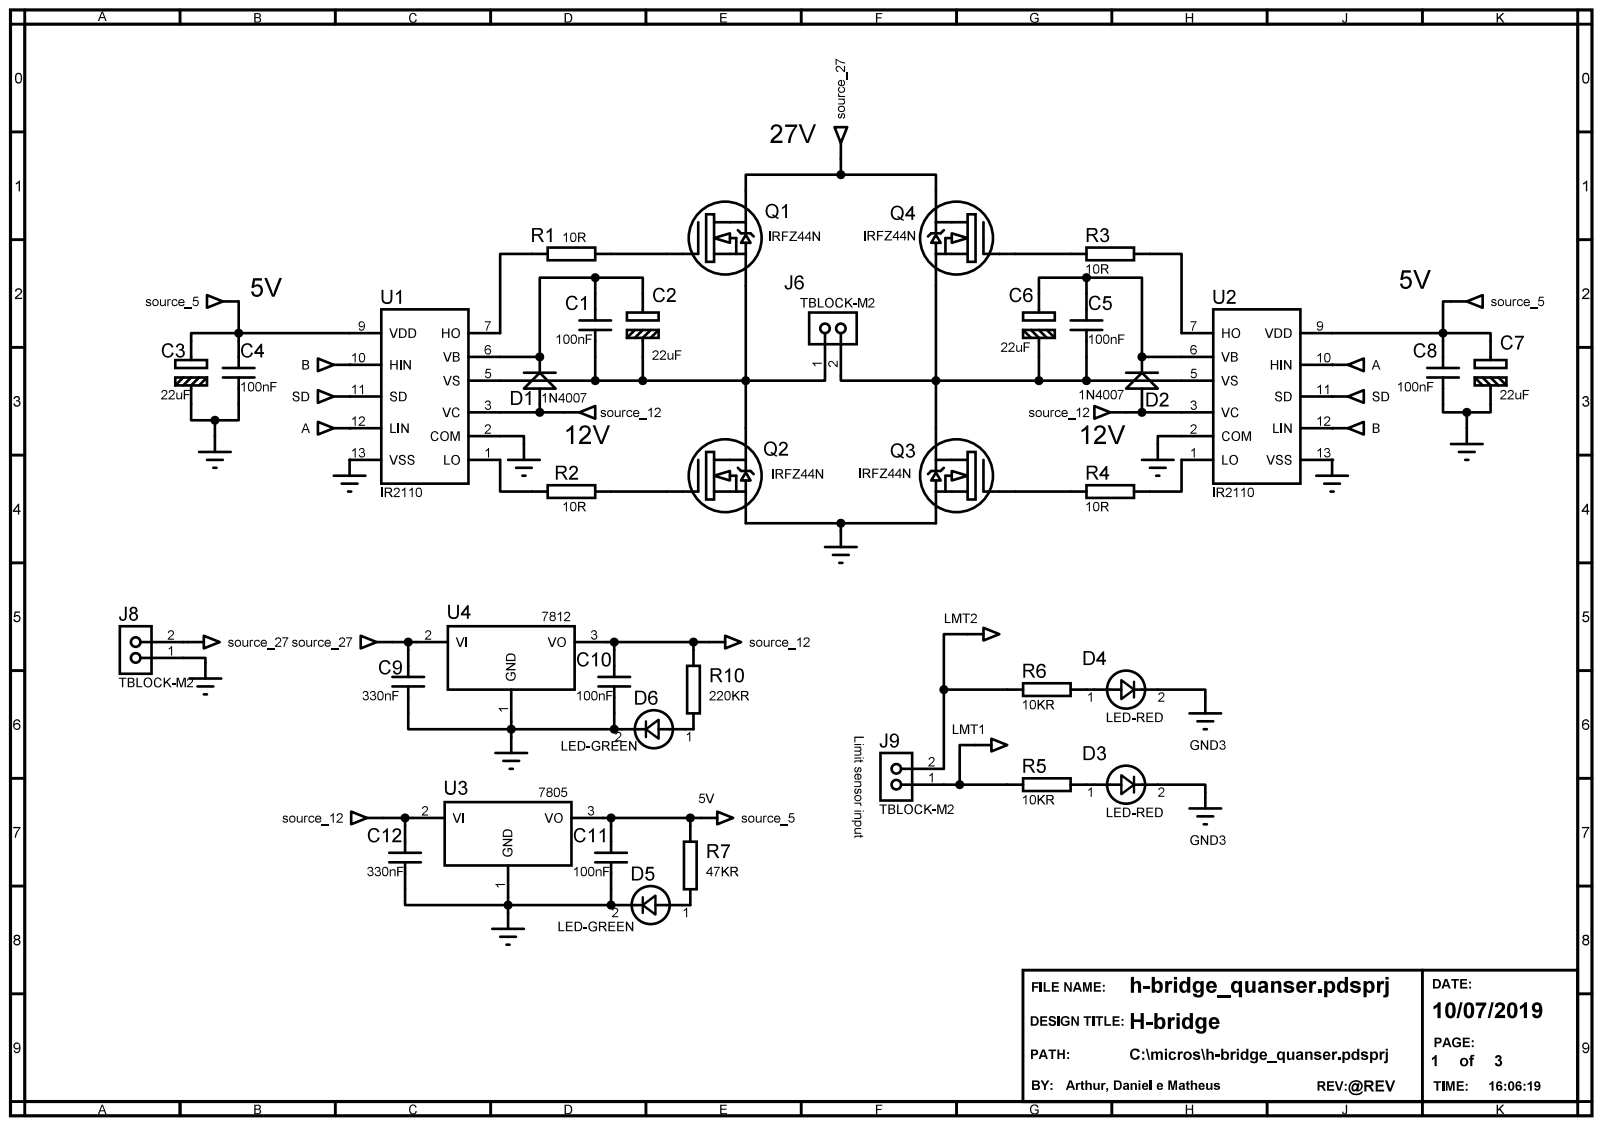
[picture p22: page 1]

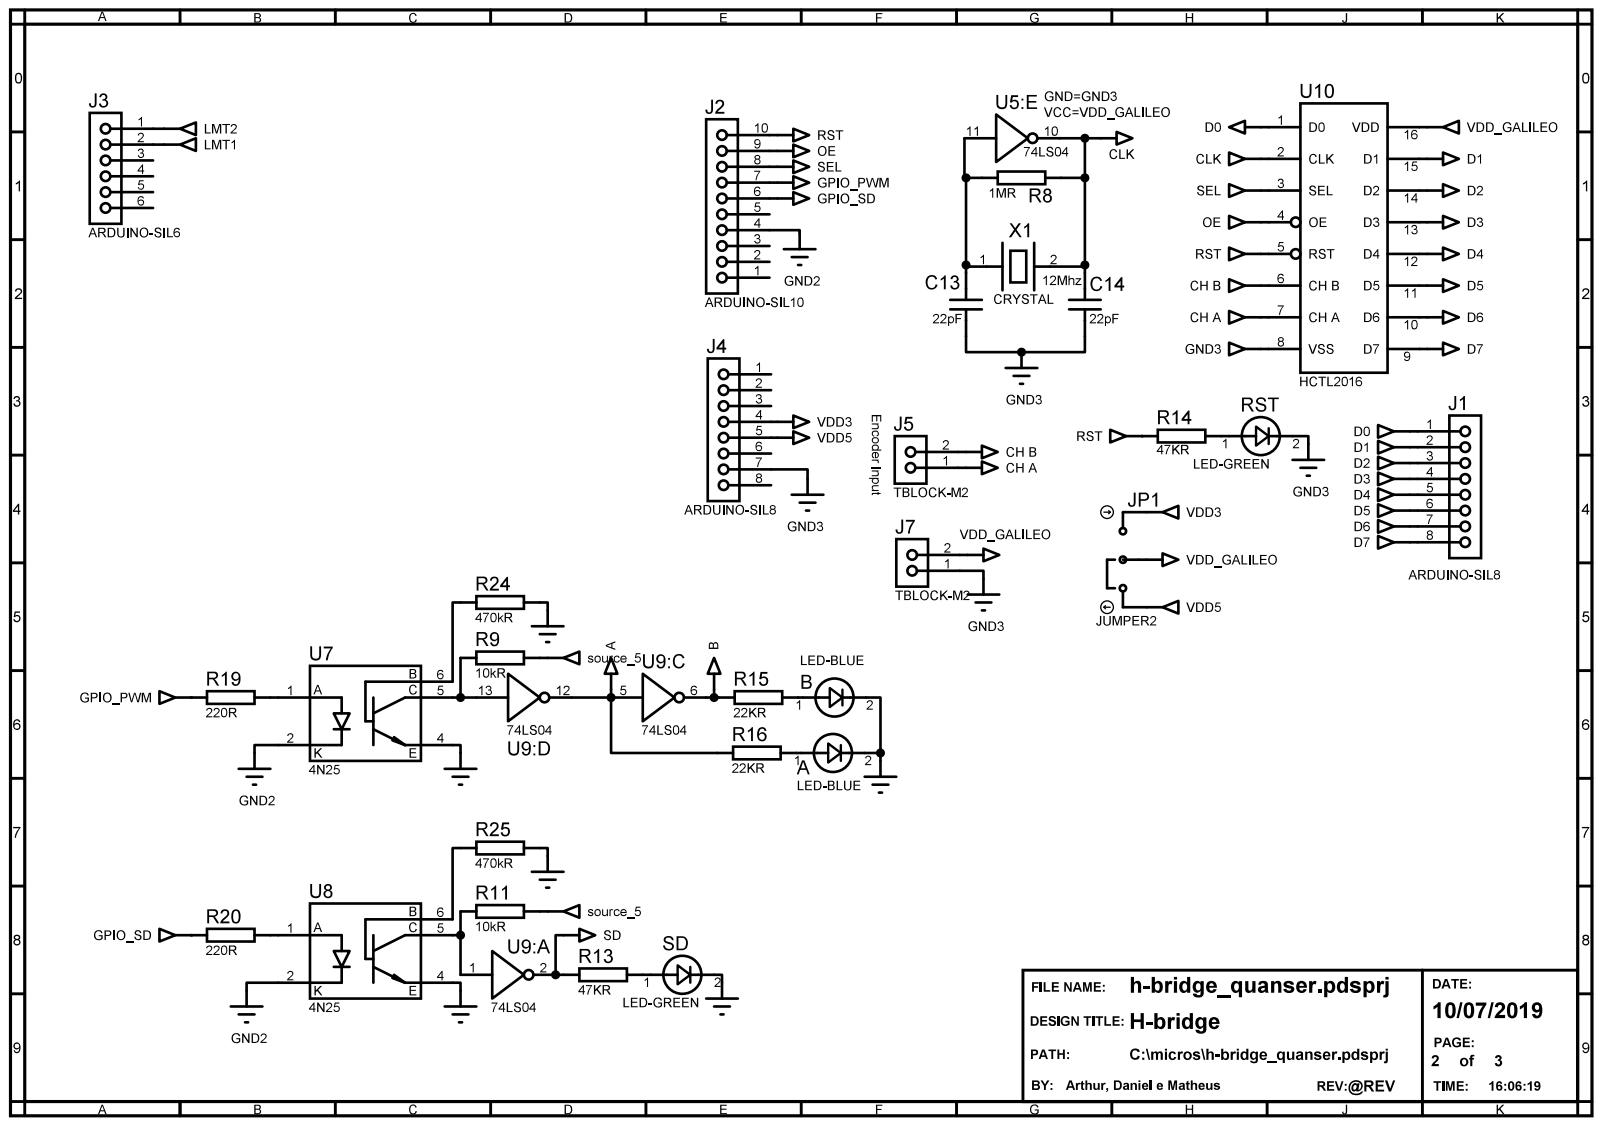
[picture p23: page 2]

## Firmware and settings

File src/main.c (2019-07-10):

/*
 * ============================================================================
 *
 *       Filename:  main.c
 *
 *    Description:  Main file of the project
 *
 *        Created:  16/06/2019
 *       Compiler:  gcc
 *
 *         Author:  Matheus Toazza Tura
 *                  Daniel Maia Cunha
 *                  Arthur Ribeiro
 *
 *   Organization:  UFRGS
 *
 * ============================================================================
 */
#include <stdio.h>
#include <stdlib.h>
#include <time.h>
#include <unistd.h>
#include <math.h>
#include "calibrate.h"
#include "args.h"
#include "colors.h"
#include "gpio_table.h"
#include "decoder.h"
#include "pwm.h"
#include "limit_switch.h"
#include "motion.h"
#include "galileo2io.h"

int main(int argc, char* argv[])
{
    /* Read command line options */
    options_t options;
    // signal(SIGINT, intHandler);
    write_pin(SD_PIN,GPIO_HIGH);
    write_pin(RST_PIN,GPIO_HIGH);
    options_parser(argc, argv, &options);
  #ifdef DEBUG
      fprintf(stdout, BLUE "Command line options:\n" NO_COLOR);
      fprintf(stdout, BROWN "help: %d\n" NO_COLOR, options.help);
      fprintf(stdout, BROWN "version: %d\n" NO_COLOR, options.version);
      fprintf(stdout, BROWN "use colors: %d\n" NO_COLOR, options.use_colors);
      fprintf(stdout, BROWN "filename: %s\n" NO_COLOR, options.file_name);
  #endif
    int decoder_reg = load_calibration();
    printf("\n");
    printf("DECODER_VALUE %d  \n", decoder_reg);
    printf("ANGLE %f rads\n", (float)2*M_PI*decoder_reg/QNSR_RESOLUTION);
    printf("ANGLE %f degrees\n", (float)360*decoder_reg/QNSR_RESOLUTION);
    return EXIT_SUCCESS;
}

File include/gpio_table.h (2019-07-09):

/*
 * ============================================================================
 *
 *       Filename:  gpio_table.c
 *
 *    Description:  Main file of the project
 *
 *        Created:  17/06/2019
 *       Compiler:  gcc
 *
 *         Author:  Matheus Toazza Tura
 *                  Daniel Maia Cunha
 *                  Arthur Ribeiro
 *
 *   Organization:  UFRGS
 *
 * ============================================================================
 */

#include <string.h>
//#include <galileo2io.h>

#define GALILEO_DUMMY_DEVICE "/home/human/Documents/UFRGS/MICROS/galileo-dummy-device"
#define PWM_CLASS_PATH "/sys/class/pwm/pwmchip0"
#define GPIO_CLASS_PATH "/sys/class/gpio"
#define GPIO_EXPORT_PATH GPIO_CLASS_PATH "/export"
#define GPIO_UNEXPORT_PATH GPIO_CLASS_PATH "/unexport"
#define GPIO_LOW "0\0"
#define GPIO_HIGH "1\0"
#define GPIO_PULLDOWN "0\0"
#define GPIO_PULLUP "1\0"
#define GPIO_OUT "out\0"
#define GPIO_IN "in\0"
#define NONE 2
//#define RESOLUTION ot@.2
#define RESOLUTION 1365 //PPR
#define QNSR_RESOLUTION 4096 //counts per quadrature

#define D0_PIN 0
#define D1_PIN 1
#define D2_PIN 2
#define D3_PIN 3
#define D4_PIN 4
#define D5_PIN 5
#define D6_PIN 6
#define D7_PIN 7

#define RST_PIN 8
#define OE_PIN 9
#define SEL_PIN 10
#define SD_PIN 12

#define LMT_SWITCH_R 15
#define LMT_SWITCH_L 14

// configure the chosen pin
// pin: from 0 to 19
// res: GPIO_LOW or GPIO_HIGH
// dir: DIR_OUT or DIR_IN
int set_pin(int pin, char*  res, char* dir);
int write_pin(int pin, char*  value);
char* read_pin(int pin, char* str_pin_data);
void initialize_gpio();

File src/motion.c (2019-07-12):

#include <stdlib.h>
#include <stdio.h>
#include <time.h>
#include <math.h>
#include <signal.h>
#include "decoder.h"
#include "control.h"
#include "gpio_table.h"
#include "pwm.h"
#include "limit_switch.h"

static volatile int keep_running = 1;

void stop(){
  set_duty_cycle(50);
  usleep(100);
  write_pin(SD_PIN, GPIO_HIGH);
  disable_pwm();
}

void signal_handler() {
    keep_running = 0;
    stop();
}

int move(float voltage){
  voltage = fminf(27, voltage);
  voltage = fmaxf(-27, voltage);
  float duty_cycle = 50 + 50*(voltage)/27;

  duty_cycle = fminf(96, duty_cycle);
  duty_cycle = fmaxf(1, duty_cycle);
  set_duty_cycle(duty_cycle);
  enable_pwm();
  
  // shutdown-pin low: Turn on the bridge drivers
  write_pin(SD_PIN, GPIO_LOW);
  return 0;
}  

int move_to_angle(float angle){
  pid_control *pid = (pid_control*)malloc(sizeof(pid_control));
  int lmt_left = 0;
  int lmt_right = 0;
  clock_t last, now;
  float current_position = 0;
  float error = 0;
  int last_dec = 0;
  int now_dec = 0;
  int overflow_count = 0;
  int decoder_reg = 0;
  int max_value = load_calibration();
  
  int result = load_pid(&pid->kp, &pid->ki, &pid->kd);
  angle = fmod(angle, 360);
  angle = 2*M_PI*angle/360;
  if (result == 0){
    last = clock();
    current_position = 0;
    int print_count = 0;

    signal(SIGINT, signal_handler);

    last_dec = read_decoder();
    while(keep_running){
      
      
      
      
      now_dec = read_decoder();
      buffer_detect(now_dec, last_dec, &overflow_count);
      decoder_reg = now_dec + overflow_count*65536;	
      
      current_position = M_PI*decoder_reg/max_value;
      error = angle - current_position;
      if (print_count % 10 == 0)
       printf("%d:   POS: %f  |  TARGET %f  |  ERR %f rads  |  VOL %f V  |  REG %d\n", print_count, current_position, angle, error, pid->voltage, decoder_reg);
      now = clock();
      update_voltage(pid, error, ((double)(now-last))/CLOCKS_PER_SEC);
      move(pid->voltage);
      last = now;
      print_count++;
      lmt_right = read_limit_switch_right();
      lmt_left = read_limit_switch_left();

      /*if (lmt_right == 1 && pid->voltage > 0){
         stop();
         break;
      }

      if (lmt_left == 1 && pid->voltage < 0){
         stop();
         break;
      }    */
      last_dec = now_dec;
    }
    stop();
  };
  return 1;
}

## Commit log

2019-06-18 -added gpio_table and pwm functions
2019-06-18 - fix compilation errors and warnings
    [gpio_table.c, pwm.c]
2019-06-18 - documentation header in gpio_table.c and - gpio.h constants fix
    [gpio_table.c]
2019-06-18 - fix compilation error
    [gpio_table.c, pwm.c]
2019-06-19 pullup and down resistors at pins 0 to 7
2019-06-24 refactoring and pid controller
2019-06-26 fix: bits and pins order
    - fix: bits order
    - IC signal order
    - added nanoseconds time delay
    [decoder.c]
2019-06-30 pwm read/write, added motion files, added motion and frequency terminal parameters
2019-07-01 added pid files and functions
2019-07-09 - move function given a voltage
2019-07-09 PID function typecast fixed
    [gpio_table.h, main.c, motion.c]
2019-07-09 pid numbers save and load function, -p parameter for setting pid values
2019-07-09 Revert "stop execution"
    This reverts commit 3e1f603a8531e9f10ad3b0bf28254f350fa57e62.
    [main.c]
2019-07-09 write and read error fixed
    [gpio_table.c]
2019-07-10 -fix warnings, -Makefile naming convention
    [motion.c]
2019-07-10 -radians conversion, -fix help message for PID
    [motion.c]
2019-07-10 calibration and limit switch break
2019-07-10 hardware stuff
    - netlist
    - Bill of materials
    - gerbers
    - schematic
    [h-bridge_final_14 - CADCAM Bottom Assembly.GBR, h-bridge_final_14 - CADCAM Bottom Copper.GBR, h-bridge_final_14 - CADCAM Bottom SMT Paste.GBR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]
2019-07-11 Readme.md updated
    - Schematic
    - limit switches pin numbers
2019-07-12 Fix read_angle in radians
    - fix: read_angle now in radians
    [decoder.c]
